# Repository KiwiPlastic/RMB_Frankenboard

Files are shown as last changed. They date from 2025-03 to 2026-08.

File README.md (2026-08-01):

# RMB_Frankenboard

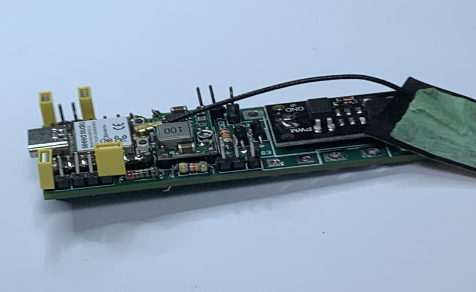
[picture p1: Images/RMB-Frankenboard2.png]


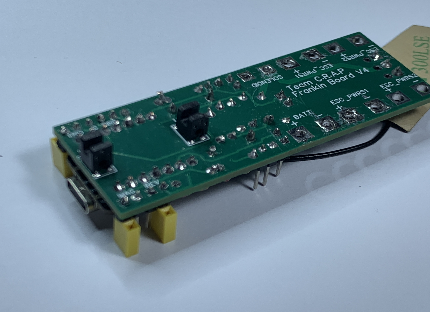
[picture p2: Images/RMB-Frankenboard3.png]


## Introduction
RMB-Frankenboard. A mix of different PCB modules hooked up, flashed and ready to go with a Signal, or Two stage brushless Nerf Blaster type build. Designed to be used with a Neutron solenoid, ramping a 30 dps plus out of the box. Comes with an esp32 MCU and optic gates on the back of PCB for the closed loop feedback.

Controlled and configuration via Blue Tooth app on your phone and a select fire switch on the blaster for fire modes on the go. 
The RMB-Frankenboard can go into any type of Nerf type Blaster with a solenoid, and brushless flywheels. This could be a factory mod, or a 3d printed Blaster.

RMB-Frankenboard is integrated into the newest version of Mjölnir evolved files, which can be found in this repository. 

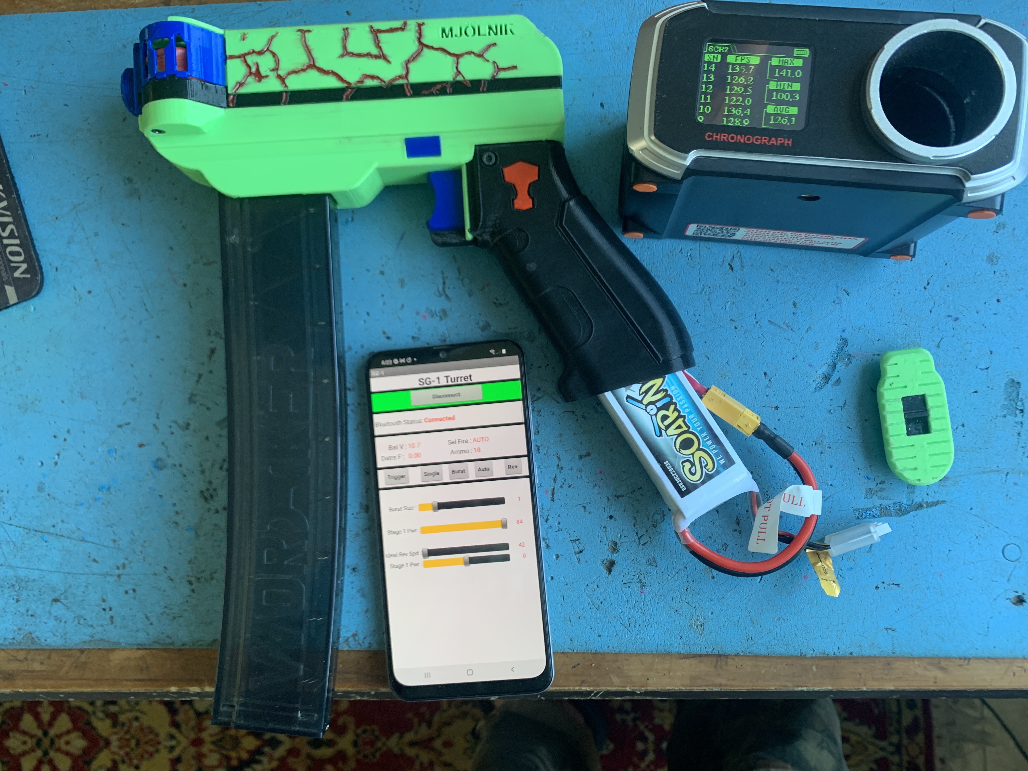
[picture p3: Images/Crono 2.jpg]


RMB-Frankenboard is actively evolving and currently consists of these Features

### Features
- RMB-Frankenboard: Seeed XIAO ESP32C3
- Supports dual Stage Brushless motors wired directly to headers on RMB-Frankenboard
- Will work with Half Darts or Long Darts
- Solenoid Pusher
- Optical Interrupt Gate on PCB for closed loop Pusher feedback. Front and Rear gates
- Single board no wiring loom
- Uses common through Hole parts and modules
- Controlled via Bluetooth App on Android phone for configuring your requirements. Download from google play store
- Battery connects directly to PCB via XT60/30
- Battery Type is auto detected. 4S-2S
- 3 Mode Select fire Switch
- Single Trigger Switch
- Rev Switch
- Magazine Sensor switch (code not completed)

- Via App: Display Battery Voltage
- Via App: Display Select Fire mode
- Via App: Display DPS
- Via App: Display Ammon Counter
- Via App: Trigger Button
- Via App: Game time countdown
- Via App: Burst Size slider
- Via App: Stage 1 Power slider
- Via App: Stage 2 Power slider
- Via App: Rev Ideal Speed slider
- Via App: Game Time slider

### Hardware Required (you supply)
 - 2 x Brushless Motors
 - 2 x ESC or quad
 - Solenoid Pusher (Neutron for Mjolnir evolved) 
 - Trigger switch NO, COM
 - Select fire, 3 position switch, NO, COM, NO
 - Rev Sw NO, COM
 - Mag Sw NO, COM
 - USB type C Data Sync lead

 - Android phone & app for configuration, else is on factory defaults.	
	NOTE: App does not work on iPhone.
	
	NOTE2: Android phone does not need to be connected to a GSM network. Frankenboard uses the phones Blue Tooth for a connection. App can be downloaded to via local Wi-Fi connection.

RMB-Frankenboard Wiring Diagram

## Getting Started - First Power Up
On receiving your RMB-Frankenboard, the first thing to do BEFORE any soldering is started, is to confirm its operation. Do not remove aerial.

First download the repository by clicking the green button over on the right says ‘CODE’ and selecting the zip.
You will also need Arduino IDE and a USB type C data sync cable

Confirm PCB operation in one of two ways: -
- Option 1. Using Phone App. 
Install App on to Android phone from this this link https://play.google.com/apps/internaltest/4701250598279133112
or use APK file in this repository to install App.

	Power up RMB-Franken board, using USB-C lead into a USB power supply or USB on a PC/Laptop
	
	Use App to connect to RMB-Frankenboard and confirm its working by scanning and connecting.

- Option 2. Using Arduino IDE. 
Plug in a USB C data sync lead (Not a charger lead) between RMB-Frankenboard and PC.
Start Arduino IDE and set serial port via tools menu to correct number	
	Open IDE serial monitor window, set board rate to 115200. You should see text output, probably "BAT low.

	If not, close serial window, try reboot by via power cycle (unplug USB lead and plug back in), immediately open serial window open, you should see quite a few lines of text on startup.

Once you have confirmed you have a working board on the bench, you can start your build. 
Install board and solder up.

## Leave one leg of Solenoid disconnected

## Optical Interrupt and Solenoid Duffer
BEFORE powering up...

- Solenoid pusher must have an aligned Duffer attached to it, for the optical interrupts on the solder side of PCB to work correctly.

- NOTE: If this is Duffer is not aligned correctly it will jam and the PCB will smoke and be damaged.

- The Solenoid PCB assembly may need to be pulled apart and put back together a few times to get the operation and tolerances correct.

- On first time assembly the Duffer will be to long.

- Manually move the solenoid in/out, noting where the Duffer touches. 

- Disassemble and file Duffer. 

- Repeat

- Once done correctly you should be able to manually push the pusher out with no resistance along its travel, until it reaches full travel and sits between the front Optic gate.
 
- Let it go slowly, and it should go back to rest between the rear Optic gate. If not dissemble and adjust. If you need to help it, it’s not correct.

- There cannot be the slightest touch between Optic gate and Solenoid Duffer. At high ROF this will course a jam and magic smoke will appear.

- Finaly, hold the pusher in the forward position and let the pusher go, in such a way that it snaps back via the spring. Ensure Duffer goes back through rear Optic gate without collision.

Tech Note: If this is not configured correctly before power up, the RMB-Frankenboard will not function correctly and could burn out.

### BLE Aerial
The BLE Aerial has a very delicate plug, we do not recommend removing it, as it may become damaged and not reconnect to PCB.
Do not power up RMB-Frankenboard without the Aerial connected, this will damage the ESP32 chip, with back RF.

## Power Up and Testing
Once wires are connected, the RMB-Frankenboard needs to be powered from a Li-po battery, to power up correctly. 

The RMB-Frankenboard uses serial output to indicate status.
We can use this to check for correct operation, before using the Trigger.

You will need a Laptop/PC with Arduino IDE running and a USB C type data sync lead, not a charger lead.

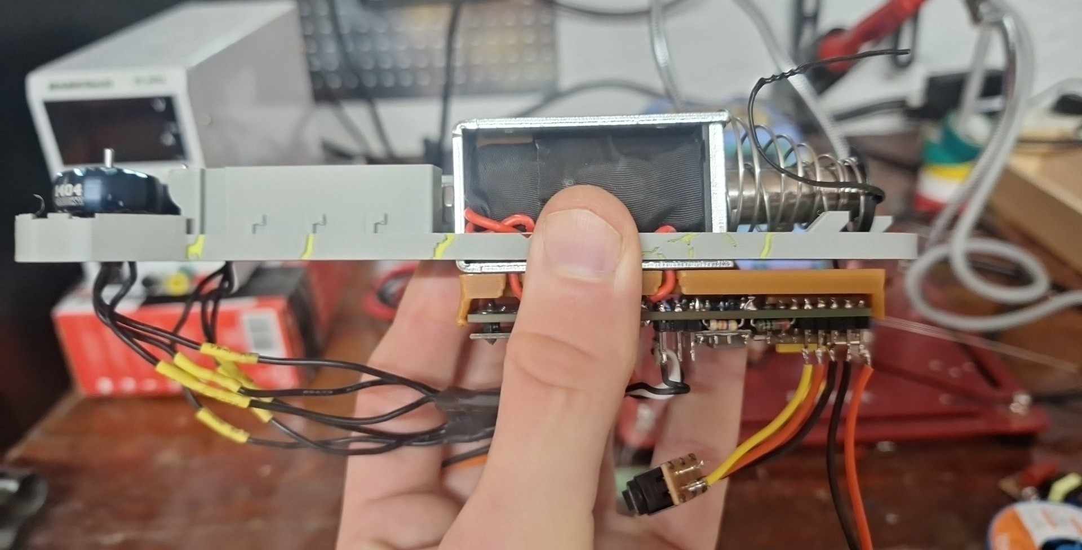
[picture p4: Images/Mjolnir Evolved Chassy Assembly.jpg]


### Plug in Li-Po battery NO USB lead
1. You should here the startup beeps of the ESC's, (Beep, Beep, pause Beep).

2. Plug in USB lead 

3. Start IDE, open serial monitor, and configure com port and baud rate 112500

4. Power cycle RMB-Frankenboard by unplugging USB and plug back in. You should see text data in the IDE serial Window.

5. Change the Select Fire Switch position. Serial Monitor will indicate switch position: - Singal Burst Auto. Leave on Singal.

6. Manually move pusher forward, while watching serial Monitor. 
Rear Optic Gate will indicate 1 and 0, push forward and Front Optic Gate will indicate 1 and 0. If there is resistance, or a tight spot, it needs to be fixed. Disassemble and adjust (file).

7. With Solenoid DISCONNECTED. 
Disconnect USB lead. 
Set Select fire switch to SINGLE shot.
While watching Mosfet pcb, pull trigger once. 
Red LED on Mosfet pcb should light bright and momentary, motors should also spin up.
Try again to be sure.
Do not move the Select Fire Switch
Disconnect battery

8. With battery disconnected, solder other solenoid wire into correct hole on RMB-Frankenboard. NO USB lead.
Reconnect battery
Pull Trigger once
Pusher should snap fast, to do a single shot and flywheels spin.
Try again x 3 or 4 times
Only if that worked, then try Burst, then Full Auto.

Tech Note: 
If something is wrong with the alignment of optic gates and the Dufa, it will do single shot slowly. Burst and full auto will drive Mosfet fully hard on (red led n) making magic smoke if solenoid is connected. 

9. Connect to RMB-Frankenboard via the app, confirm its reading battery voltage eg will be around 12v. 

### RMB-Frankenboard App and Operation
The firmware comes with default configuration setting, and will work fine without the App. 

However, if you want to change the settings or use a remote trigger you will need the app.

The RMB-Frankenboard can be set back to defaults by holding trigger while power up.

If you have purchased an RMB-Frankenboard, you can download the app from this link: -
https://play.google.com/apps/internaltest/4701250598279133112

Alternatively, the apps, apk file is also in the repository and can be installed directly to the phone.

The Android phone does not need to be connected to a GSM network. Frankenboard uses the phones Blue Tooth for a connection, not the GSM network. 
The App can be installed via local Wi-Fi connection.

The App displays status for Battery Volts, Select Fire Mode, Darts Shot,
Trigger and Start (Game Start).

### Slider Settings: -
- Burst Size
- Stage 1 ESC Power
- Stage 2 ESC Power
- Ideal Rev Speed
- Game time

In addition to Trigger and Select Fire switches the RMB-Frankenboard, supports a Rev switch and Mag switch input

### Rev Idel function
Set Ideal Rev Speed > motor stall speed for pre spin. 
First shot will activate ideal, ie its idling after the first shot
Change Select fire Mode Switch to turn ideal off until next shot

If you have a rev button it works like normal, hold it in for on.

## Fault finding
The RMB-Frankenboard has a event based serial output that can be monitored via the serial window in Arduino IDE at 15200 baud.

The serial output can be used to see that buttons, switch's etc are working.

If you cannot see the serial output, there's something not right. Power down. Does it give serial output when powered from USB only? Ie no Li-Po Battery.

## Word of warning
When you have the USB plugged in, DISCONNECT the solenoid or do not operate the trigger. 
The solenoid generates back EMF and can damage the USB port, I speck form experience.

Do not power up RMB-Frankenboard without the Aerial connected, this will damage the ESP32 chip with back RF.

This project is underdevelopment and actively evolving, please report issues so we can make improvements.

## How to Purchase RMB-Frankenboard
RMB-Frankenboard is $35usd plus shipping. 
Most countries, shipping is about $15usd (Ozy is cheaper).

Place order by contacting us via, 
Discord: Kiwi_7862
FB Messenger: Richard Fred

We require these details
- Name:
- Quanty:
- Email Address:
- Delivery address:
- Country:

We will send reply of receipt of your order
Then confirm shipping cost and send you a PayPal invoice via your email
Your email address is also used to register the Android App so u can download it from app store via supplied link. 
On receipt from PayPal that you have paid we ship.
We plan to have an Esty store shortly to make this more simple

## Flash Download Tool
This tool allows flashing of the firmware via *.Bin files.
It is a lot simpler than getting the correct libarys and a working compile from the Arduino IDE.

Firmware upgrades will be done using this tool.

The sub folder \bin in Flash download tool has the *.bin files it it.

Procedure: -
- Disconnect Li-Po Battery
- Close Arduino IDE
- Plug in USB data sync cable (not a charging cable)
- Open Flash Download Tool
- First Window Select: -
-   ESP32 C3
-   Development
-   USB

With reference to screen shoot in folder
Setup the download window. With correct path, and in this order.

 - Bootloader.bin 		0x0
 - Partions.Bin 		0x08000
 - RMB ESP32 V35.Bin 	0x010000

- 40Mhz 
- DIO
- DoNotChgBin = off
- Combine = off
- Select com port at 115200

Put chip in Bootloader mode. 
The chip has two buttons, one each side of the Arieal socket.
One is Reset = R, other is Boot = B
- Unplug USB
- While holding the B boot down plug the USB back in
- It will now power up in Bootloader mode
- Click Start…wait for green bar to move across screen
Flashing Complete

## Links
https://play.google.com/apps/internaltest/4701250598279133112

Note your email needs to be registered with us before this will work

https://github.com/KiwiPlastic/RMB_Frankenboard

https://www.arduino.cc/en/software/

## Attributions
(c) 2019-2021 Michael Ireland / Ireland Software / Airzone for example code used early on in project development work.
BLE Server examples
    Based on Neil Kolban example for IDF: https://github.com/nkolban/esp32-snippets/blob/master/cpp_utils/tests/BLE%20Tests/SampleNotify.cpp
    Ported to Arduino ESP32 by Evandro Copercini
    updated by chegewara and MoThunderz
	
## Licensing
Non-commercial license is in effect. This license flows to derivative works.
You are free to remix / modify the blaster as you see fit. Please share
If you post a remix, please link back to the original.
Commercial use is allowed with the purchase of a RMB-Frankenboard at a ratio of one board = one commercial build.

## 📜 License
RMB-Frankenboard
by Team C.R.A.P is licensed under the Creative Commons Attribution - Non-Commercial Licence. Zero v1.0 Universal License. See `LICENSE` for more information.

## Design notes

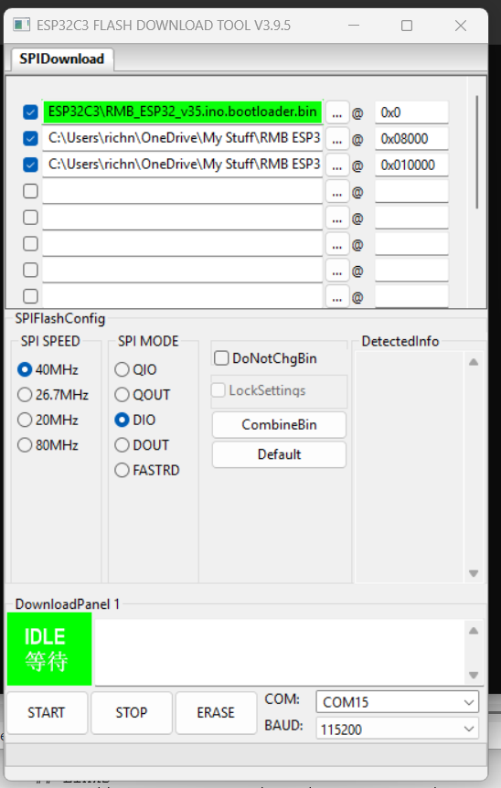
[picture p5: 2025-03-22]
Code/flash_download_tool_3.9.5/Flash downlaod tool.png

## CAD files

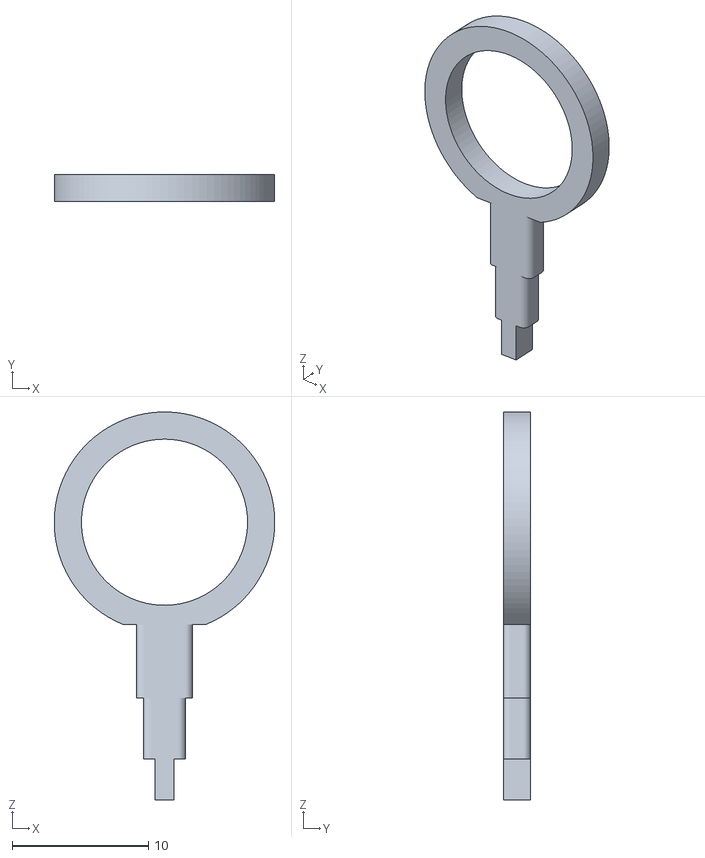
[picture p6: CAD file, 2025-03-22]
3D Prints - Mjolnir Evolved/Solenoid ring By Genexis.stl
16.2 x 2.00 x 28.5

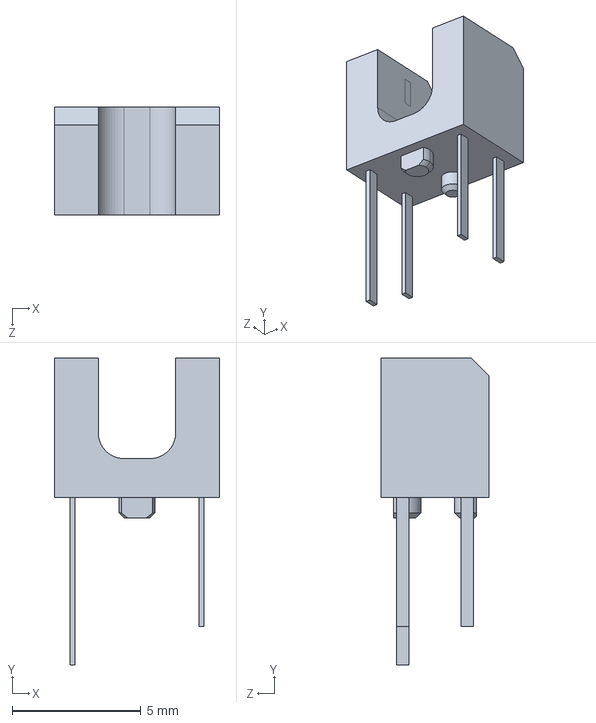
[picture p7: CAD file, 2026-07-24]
PCB/RPI-352.STEP
6.40 x 11.9 x 4.20 mm

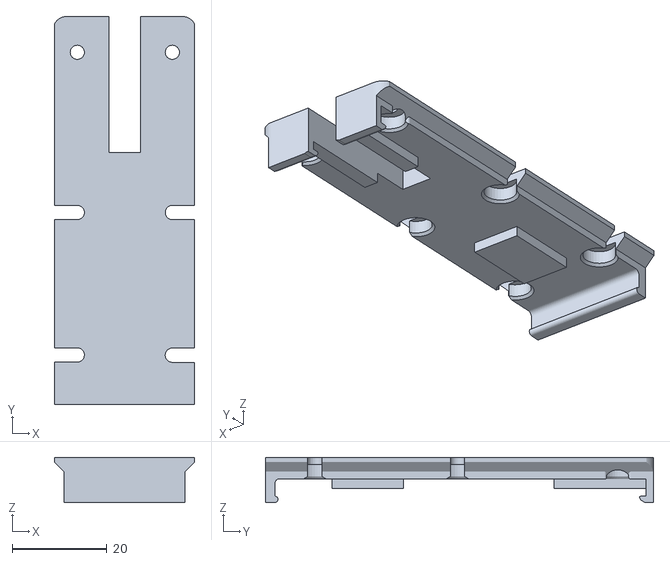
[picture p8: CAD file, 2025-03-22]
3D Prints - Mjolnir Evolved/Solenoid mount by Genexis.stl
29.5 x 81.8 x 9.50

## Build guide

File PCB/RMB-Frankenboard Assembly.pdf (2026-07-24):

## Team C.R.A.P RMB – Frankenboard

What is it
RMB-Frankenboard. A mix of dierent pcb modules hooked up, flashed and ready to go with a brushless build. Ment to be used with a neutron solenoid ramping a 30 dps out of the box. Comes with an esp32 MCU and optic gates on the back for the feedback. Controlled via BT app on your phone and a select fire switch on the blaster for fire modes on the go.
Integrated into the newest version of Mjölnir evolved

Features
- 2 Stage Brushless motors wired directly to RMB-Frankenboard
- Foam Projectiles, Half Darts or Long Darts you could also potentially use rival balls or disks
- Solenoid Pusher
- Optical Interrupt Gate on PCB for closed loop Pusher feed back. Front and Rear gates
- Single board no wiring loom
- Uses common through hole parts and modules
- Controlled via Bluetooth App on Android phone for configuring your requirements. Download from google play store
- Battery connects directly to PCB via XT60/30
- Battery Type is auto detected. 4S-2S
- 3 Mode Select fire Switch
- Single Trigger Switch
- Rev Switch
- Magazine Sensor switch (Future program upgrade)
- Set to defaults by holding trigger while power up
- Via App: Display Battery Voltage
- Via App: Display Select Fire mode
- Via App: Display DPS
- Via App: Display Ammon Counter
- Via App: Trigger Button
- Via App: Game time countdown
- Via App: Burst Size slider
- Via App: Stage 1 Power slider
- Via App: Stage 2 Power slider
- Via App: Rev Ideal Spd slider
- Via App: Game Time slider
- To be added to app: Select fire Switch
- To be added to app: Rev Button
- NOTE: The App, does not work on a iPhone, it’s very expensive to get a dev licence.

Licensing
Non-commercial license is in eect. This license flows to derivative works.
Commercial use is allowed with the purchase of an RMB-Frankenboard from our Store at a ratio of one board = one commercial build.

Attributions
BLE Server examples
Based on Neil Kolban example for IDF: https://github.com/nkolban/esp32-snippets/blob/master/cpp_utils/tests/BLE%20Tests/SampleNotify.cpp Ported to Arduino ESP32 by Evandro Copercini
Updated by chegewara and MoThunderz
(c) 2019-2021 Michael Ireland / Ireland Software / Airzone for example code used early on

License
RMB-Frankenboard
by Team C.R.A.P is licensed under the Creative Commons - Attribution - Non-Commercial Licence
https://creativecommons.org/licenses/by-nc/4.0/

Introduction
This is an advanced project, which requires some experience in electronics to complete. You can purchase the Assembled and tested RMB – Frankenboard from our website site, we recommend this, to minimize frustrations in getting it going.
Please read, all documentation before starting this project.
Documentation:
- Frankenboard assembly, This file.
- RMB_ESP32_vnn.ino Arduino file. Read the header,.
- README.TXT, for helpful information.

FLASHING the ESP32 chip
Before starting this project, you need to flash the ESP32 chip, brand new out of the packet, while it has no wires or soldering done to it. This is very important, as you need to know the chip is working before you solder to it.
If you are not familiar with this procedure for the ESP32, we suggest you purchase the chip only before any other parts. Then flash the chip with the Arduino file.
NOTE you need a Micro USB-C with DATA SYNK cable. Not a phone charger cable.
Basic procedure: -
- Install Arduino IDE
- Load correct Board Library, XIAO ESP32 - S3, or XIAO ESP32 – C3
- Load required library’s, into IDE for the code to compile. It will tell you what libarys it wants
- Get a successful compile
- Upload code (Flash chip)
After flashing, check for serial output in the IDE serial window, 115200 Baud, it will say BAT LOW.
If you get to this point, you have proven you have a ‘working’, RMB ESP32 chip.
Connect Blue Tooth aerial, load app to Android phone, Test app connection and operation.

If your having trouble flashing the ESP32, we recommend buying the assembled RMB-Frankinboard from our webpage.

BOM

### 1 x Micro USB-C Data Sync lead

### 1 x RMB-Frankenboard PCB 77 x 27mm 4 Layer

### 1 x U1 – Seeduino Xiao ESP32-S3. (C3 will work but is significantly slower)

### 1 x U2 - LR7843 Mosfet module

### 1 x U3 - MP2307DN 17x12mm Mini Buck, 5v (adjustable ones can vibrate and might be

unreliable).

### 2 x U4, U5 – RPI-352 Optical Interrupter

### 2 x IN4007 Diodes D1, D2

### 2 x 22K Resistor R5, R8

### 2 x 330R Resistor R3, R6

### 1 x 47K Resistor R1

### 3 x 10K Resistor R2, R4 & R7

### 1 x XT60 Male plug

### 40 x 1 Pin Header Strip

The ESP32, Buck, and Mosfet module, mount via soldered pin headers.
The PCB is laid out to take standard size sockets and plugs.
Plugs and sockets introduce an unreliability in our finished product. I prefer to solder all wiring connections except the ESC signals. I use a 2-pin header for the ESC1 and ESC2 parts, as the ESC normally has a 2 or 3 pin socket on its lead.

Assembly
At this point you should have a Firmware flashed RMB-ESP32
The order of putting parts on this PCB is important, as they go on both sides, and some solder points will not be accessible when other parts are mounted. All leads going through the PCB should be cut as short as possible.
Bottom side
Install the 2 x RPI-352 Optical Interrupter (Note the orientation). The bevelled corner faces the USB-end of the PCB.
The component on the KY-010 interrupter module can be used, if you remove it

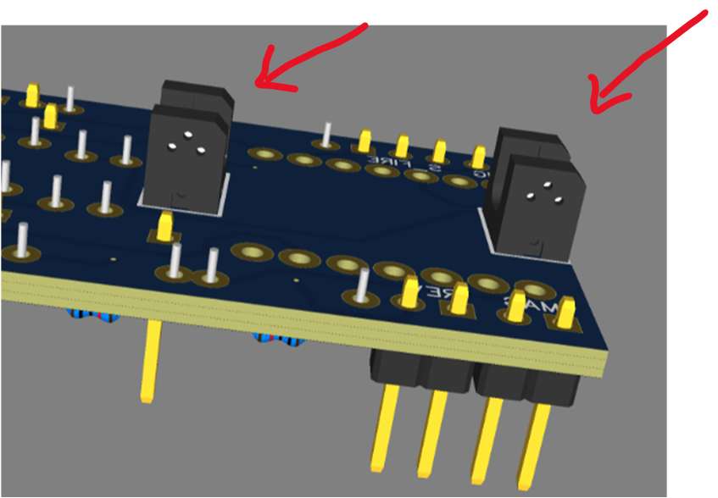
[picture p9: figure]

Top Side

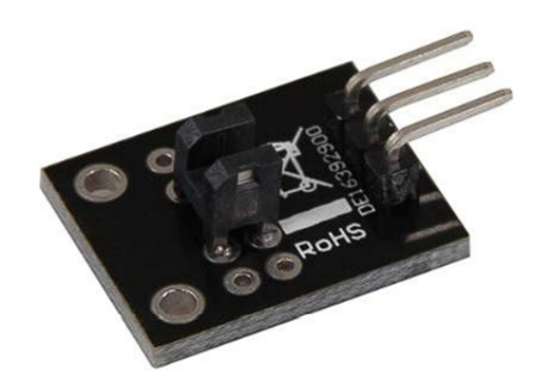
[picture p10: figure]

Next install top side resistors and diodes (Note the direction of the diodes). See diagram
below. | Red lines = Limit input test points

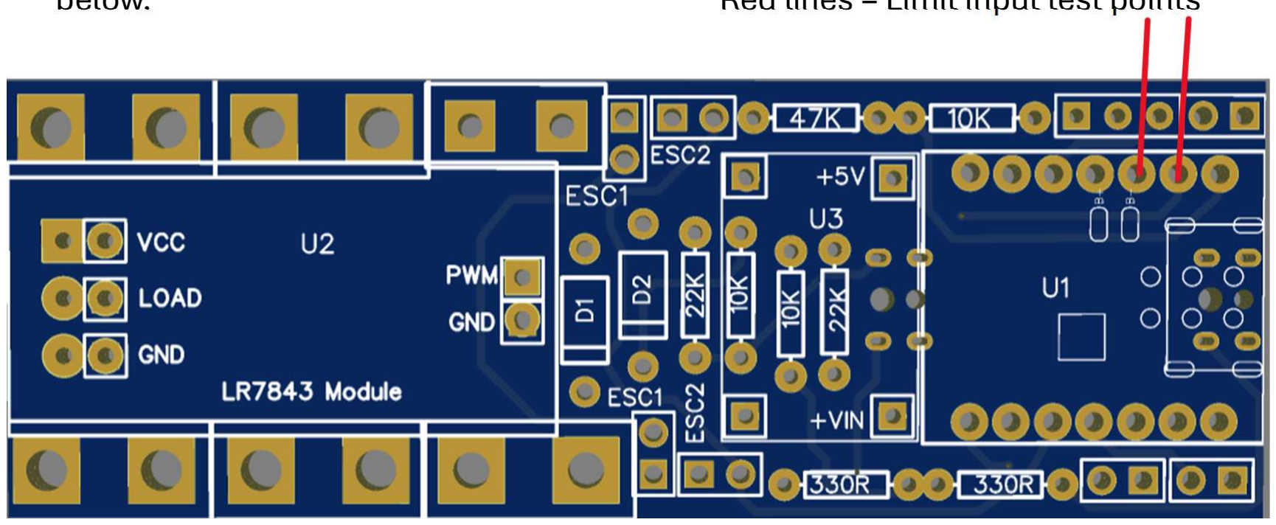
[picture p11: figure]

Mini Buck
This mounts on 4 header pins. Cut 4 single pin headers o pin header strip. Place long end of pin into Frankenboard x 4.
Then place Buck module on top, hold assembly together and solder.
Cut o long legs from underside of Frankenboard.

First Power Up Test 1
Connect a XT60 to the Bat pads (GND on left POS on Right) and plug in Lipo Battery. Using multi meter cheek between GND and 5v pin on ESP32 pad, should be 4-5v.
If Adjustable Buck, set output to ~5.7v as required to get 5.0v at ESP32 5v pin.
Measure between GND and PIN 2 (front limit gate) & PIN 3 (rear limit gate) (see red lines on pic above). Use a bit of tape to slide between interrupters. Voltage will be 0V open and 3V when interrupted
Disconnect battery.
ESP32
This mounts on 2 x 7way pin header strips. Cut 2 strips of 7 pins.
Insert long end of pin header strips into Frankenboard, ESP32 location.
Place ESP32 chip on top. It is keeping the pins in alignment for soldering to the Frankin PCB.
Hold assembly together and solder the pin header to Frankin PCB. Hint solder corner pin first then the rest of the pins. Then solder EPS32 to the pins.
Cut legs o from underside of PCB.
Install Pin Headers: -
Rev/Mag, 4 way
Trigger, 2 way
Select Fire Switch, 3 way
ESC1 and ESC2, 2 x 2 way left hand side, 2 x 2 way right hand side Mosfet Module
This mounts on 5 pins. Cut 1 pair, and 3 single pins
Insert long end of pins into Frankin PCB
Place Mosfet module on top
Do NOT solder Mosfet Module on to any pins, yet.
Hold assembly together and solder pins to bottom side of Frankenboard, only Remove Mosfet Module
Cut legs o from underside of PCB

Power Up Test 2
Do not connect any other wires yet. Do not connect USB to computer yet.
Start Arduino IDE, open serial window at 11520 baud and have USB-C cable ready, DO NOT plug into ESP32 yet.
Connect a Li-Po battery to the XT60 connector, and power up from Li-Po.
Now connect to USB-C and monitor serial window.
Do you have some serial output on screen that is readable.
Using Jumpers, on the pin headers, observe serial output and test:-Trigger Switch
Mag Switch
Rev Switch
Select Fire Mode
Remove USB cable first then lipo Battery. Final wiring
Insert Mosfet Module onto its pins and solder. Connect ESC power cables and Solenoid.
ESC Configuration
The RMB - Frankenboard accommodates Single stage and Dual stage Flywheel/ESC configurations.
Single stage
Simply plug each ESC signal cable into the connections for ESC1 on LHS and ESC1 on RHS. Solder power wires into ESC Pwr connections.
Dual Stage
As above plus, ESC2 on LHS and ESC2 on RHS. Solder power wires into ESC Pwr connections.
The RMB – Frankinboard is tested for up to XX amps, 14 volts 4S lipo battery.
Final Power Up Test 3
Hold trigger down while you connect lipo battery. This clears and defaults the memory settings.
All going well you will hear the startup beeps of your ESC’s.
Using a jumper, on the select fire pins put it into single fire mode (jumper on furthest pins from USB).
Momentarily try a trigger test. Mosfet led should turn on.

Wheels should spin and solenoid will fire.
If this doesn’t happen, it would indicate a fault. Disconnect the battery and start searching for the fault.

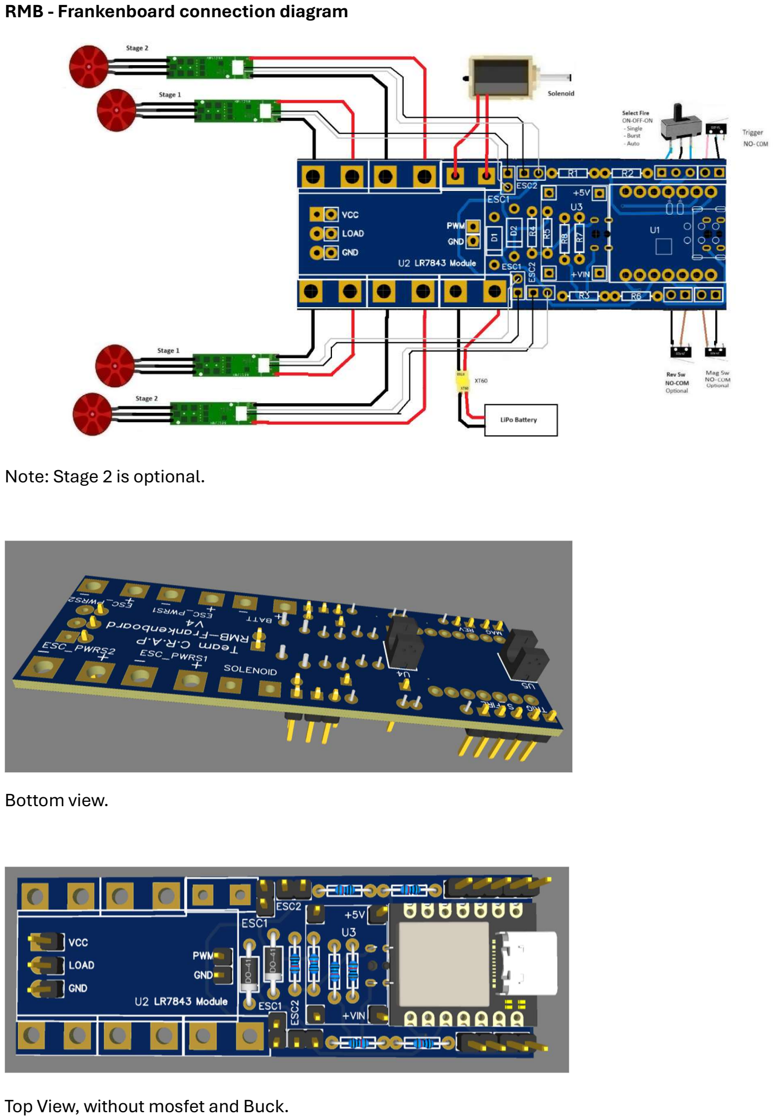
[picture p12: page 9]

RMB - Frankenboard connection diagram

Note: Stage 2 is optional.

Bottom view.

Top View, without mosfet and Buck.

RMB-Frankenboard Schematic:

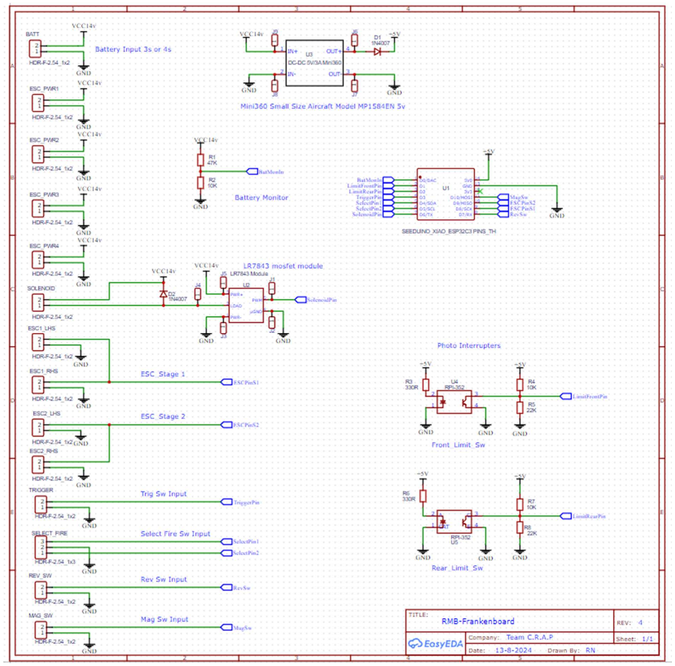
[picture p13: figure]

Flashing the ESP32 when fully wired
To ensure that the chip is in the correct boot mode please use this procedure: The chip can appear to have stopped working if not done correctly.
1. Power up RMB-Frankenboard by Lipo battery.
2. Plug in USB Cable.
3. Start IDE and chk for serial coms is present. Pull the trigger.
4. Unplug the Lipo battery.
5. In IDE select download, program will compile and download.
6. Select serial coms and check output. First line on boot is the version number.
7. Unplug USB.
8. Plug in Lipo and test.

Alternative Limit Switch wiring
If you need to use physical limit switches. This can be accomplished by removing the Photo Interrupter gates, and connecting two wires to the pads indicated, to go to limit switch front and back.

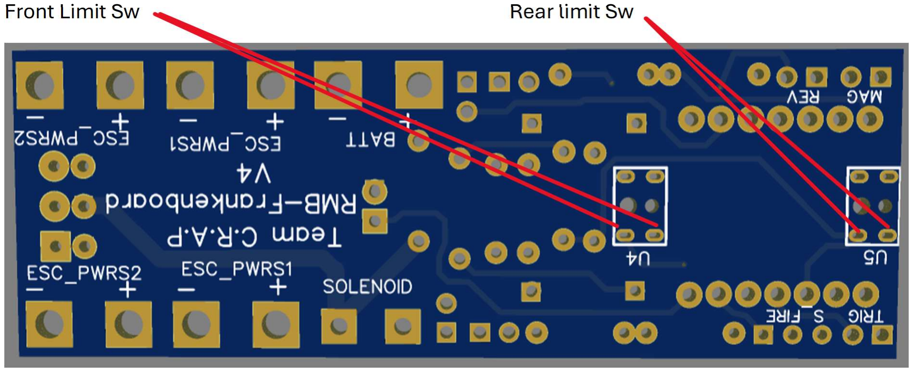
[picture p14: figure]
Front Limit Sw; Rear limit Sw

Useful Links

XIAO ESP32-S3
https://www.seeedstudio.com/XIAO-ESP32S3-p-5627.html

XIAO ESP32 -C3
https://www.seeedstudio.com/Seeed-XIAO-ESP32C3-p-5431.html

Mini Buck, 5v (Do not get adjustable) https://www.aliexpress.com/item/1005006486270630.html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

RPI-352 Optical Interrupter https://www.aliexpress.com/item/1005005805132173.html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 14ad0a98656d2fa166d47-1725070500008-06900-_mqhl1uU&tt=MG&fbclid=IwY2xjawE_W_NleHRuA2FlbQIxMAABHcbLkNNCJgfF3SDu6Kb4BOW r-iAxv--
OOrpo1Etl7_rb7eyO5_8E4jNRHw_aem_Lnkp_anG8G9avq1Bz7w9yQ&a_fsk=_mqhl1uU&a_pl atform=default&sk=_mqhl1uU&a_trace_key=225def8a69d14ad0a98656d2fa166d47-1725070500008-06900-
_mqhl1uU&shareId=21610518952&businessType=ProductDetail&platform=AE&terminal_id=18 184d2796b14b49999ce2660aa4400a&afSmartRedirect=y&gatewayAdapt=4itemAdapt

KY-010 Optical Interrupter can be used by removing part https://www.aliexpress.com/item/1005006290314720.html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 geLogUid=0fXz8dX2Bgrf&utparam-url=scene%3Asearch%7Cquery_from%3A

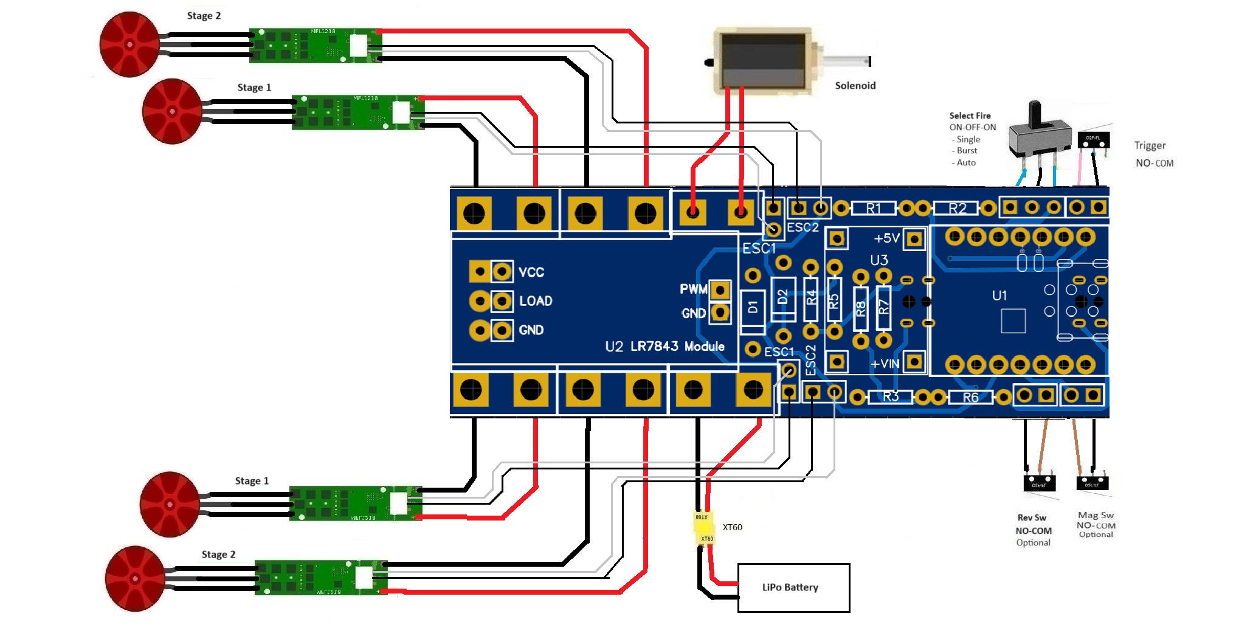
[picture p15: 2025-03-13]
Images/RMB-Frankenboard Wiring Diagram.png

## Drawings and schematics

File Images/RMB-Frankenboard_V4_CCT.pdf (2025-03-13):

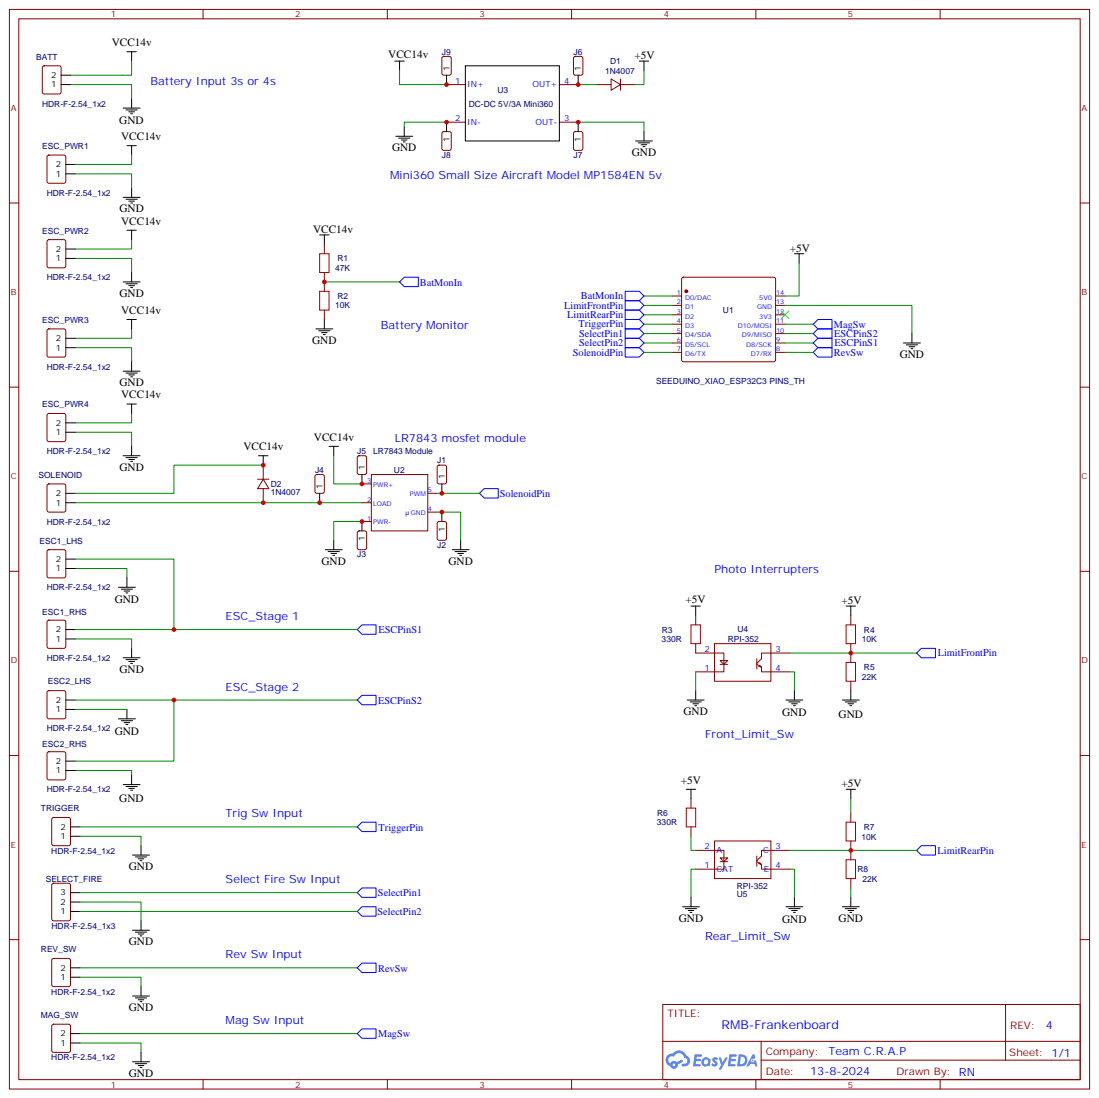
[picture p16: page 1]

GND
Mini360 Small Size Aircraft Model MP1584EN 5v

Select Fire Sw Input

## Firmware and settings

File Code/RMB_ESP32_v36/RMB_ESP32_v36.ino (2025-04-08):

#define VERSION 36
/* 8-4-25

RMB written By RICHRD NICHOLSON from NEW ZEALAND

Licensing

Non-commercial license is in effect. This license flows to derivative works.
You are free to remix / modify the blaster as you see fit. Please share.
If you post a remix, please link back to the original
Commercial use is allowed with the purchase of a RMB-Frankin-board at a ratio of one board = one commercial build

Attributions
(c) 2019-2021 Michael Ireland / Ireland Software / Airzone for example code used early on
For BLE Server examples
    Neil Kolban example for IDF: https://github.com/nkolban/esp32-snippets/blob/master/cpp_utils/tests/BLE%20Tests/SampleNotify.cpp
    Ported to Arduino ESP32 by Evandro Copercini
    updated by chegewara and MoThunderz

License
RMB-Frankin Board
by Team C.R.A.P is licensed under the Creative Commons - Attribution - Non Commercial Licence
https://creativecommons.org/licenses/by-nc/4.0/

Summary
  This code is for a Signal, or Two stage Brushless Nerf type Blaster. Using a solenoid pusher with closed loop feedback sensors
  It uses a three position switch for select fire
  Configuration is via a Android phone app

Hardware
 - Seeed XIAO ESP32C3 or Seeed XIAO ESP32S3
 - Brushless 
 - Solenoid Pusher 
 - Single-Stage Trigger 
 - 2 x limit Switch's,  to make closed loop Solenoid = High ROF
 - Select fire, 3 position switch
 - Mofet PCB, for Solenoid
 - 2 x ESC
 - 1 x Buck voltage regulator

 - Android phone app (BLE Server) does not work on iPhone

Getting Started:
  This is an advanced project. 
  We recommend Flashing the ESP32 before doing anything else. This can save you money
  If you can not get this done you wont move forward.

  NOTE: You need a USB lead that supports data, NOT a phone charger lead which do not transfer data and are common

  https://wiki.seeedstudio.com/XIAO_ESP32C3_Getting_Started/

  Arduino IDE 2.2.1
  Select Board Manger, from menu on left of screen (2nd one down)
  look for esp32 by Espressif Systems, select install, could take a little while 
 
  Libary for ESC's:
  Select Libaray manager, from menu on left of screen (3rd one down)
  Type in ESP32, then scroll down and look for ESP32Servo By Kevin Harrington
  Alternative Method:
  https://github.com/Dlloydev/ESP32-ESP32S2-AnalogWrite
  Download and install via Sketch/Include Libary/Add .Zip Libary

  Libary for PCF8575 Expander:
  Select Libaray manager, from menu on left of screen (3rd one down)
  Typ in Adafruit PCF8574 then select it 
  Alternative Method:
  https://github.com/adafruit/Adafruit_PCF8574
  Download and install via Sketch/Include Libary/Add .Zip Libary
  
*FLASH ESP32 - No WIRES connected
  It is highly recommended that you flash the firmware before you wire anything up to ensure you have a working chip
  This firmware has feature select options, please read past the libary files to see options

  While the chip has no wires on it, it will start and work with the phone app
  Bat Flat on the Serial Monitor (115200 baud) is RMB looking for the 2s/3s/4s battery on D0, Put 47k/10K on and a Bat and it will work
  The code works out what Type your battery is

*FLASH ESP32 WIRES connected
  Once wired with ESC etc... 
  Power from LiPo Bat, FIRST, then plug in USB to laptop
  The ESP32 will not start if the ESC are not powered up first, ie plugging in a USB first is a fail. Its a bootstrapping thing
  Ensure the MOSFET/Solenoid is disconnected. before Flashing firmware, it can activate and possibly make magic smoke

  Other Notes
  The Phone app has a demo mode switch so it can show the connected screen, when its not connected

  Mosfet (pusher output D10)  must be a 2-3v Gate. 5v gate ones will not work

  D8/D9 Bootstap pins must be high at Power Up/Boot
  We are using Boot strapping pins for ESC output,
  ESCs need to be powered up to get a boot if there signal wires are connected to ESP32. Else will look dead.
  Can be powered up with no ESC's if signal wires are not connected

  BLE (Bluetooth Low Energy) this is different to the older Blutooth 2.0 serial and not compatableSupports Rev Ideal mode, set RevIdeal >90 for pre spin. Change Select fire Mode Switch to turn off RevIdeal


 
  //------------------ Dev Notes -----------------------------------------------------
   ESC HW
    ESC frq = 48Khz
    ESC min Trotel = 1040 (1 milisecond)
    ESC Max Trotel = 1960  (2 Millisecond)
    8 bit PWM resolution 0 = 254

   PWM Values for this code
   freq = 1000. 1kHz dont no why, but it works
    42 = off
    45 is lowest ideal speed, lower stalls
    84 is highest speed = ESC Max Trotel, can make number higher but it does  not go any faster

  //------------------------------------------------------------------------------------------------------------------------------------------------
*/
//================================================================================================================================
//Load libraries

#include <ESP32Servo.h>                  // ESC  libary by Kevin Harrington 
ESP32PWM ESC1pwm;                        // 
ESP32PWM ESC2pwm;                        // 

#include <BLEDevice.h>                   // Blue Tooth Libary
#include <BLEUtils.h>
#include <BLEServer.h>
#include <BLE2902.h>

#include <Preferences.h>                 // ESP flash Storage Libary
Preferences preferences;


//==================================================================================================================================================
//               DEFAULT SETTINGS - USER EDITABLE DEFAULT VALUES - Saved to Flash, as default blaster settings. Hold down trig at power up

#define BURST_SIZE 4            // Burst Mode Size #number of darts
#define MOTOR_ESC1_PWR 84       // Stage 1 : ESC1 Defualt Setting Range: 45-84 max
#define MOTOR_ESC2_PWR 84       // 42 = Stop, 45 = Slow idel Rev, 84 = Full Speed
#define MOTOR_REV_IDEAL 42      // 42 = Stop, 45 = Slow idel Rev, 84 = Full Speed
#define MOTOR_MIN_SPEED 45      // 42 = Stop, 45 = Slow idel Rev, 84 = Full Speed

#define BATTERY_CALFACTOR 1.0   // Adjustment for battery calibration calibration

#define PUSHER_MAX_T 80         // ms for pusher error detect

#define MIN_DWELL_TIME 1        // NOT USED YET WIP
#define AMMO_COUNTER 18         // Mag Size, NOT USED YET WIP

//====================================================================================================================================================

//--------------------------------------------------------------------------------------------------------------------------------------
// Seeed ESP32 C3 or ESP32 S3 -  Pin Definitions (BIOS)
//--------------------------------------------------------------------------------------------------------------------------------------

#define PIN_BATT_MON A0     // Bat Volts  A0/D0       IP           Analog LiPo battery reading, Resistor devideder 47K/10K
#define PIN_PUSHER_F D1     // Pusher Limit Sw Front  IP
#define PIN_PUSHER_R D2     // Pusher Limit Sw Rear   IP
#define PIN_TRIGGER D3      // Trigger                IP
#define PIN_SELF_A D4       // Select Fire A Sw       IP
#define PIN_SELF_B D5       // Select Fire B Sw       IP
#define PIN_MAG_SW D6       // Mag switch             IP           D6 should be used as O/P only, to do with boot straping - testing mag sw option
#define PIN_REV_SW D7       // RevSw   PB             IP
#define PIN_ESC_1 D8        // Stage 1 ESC output     OP           ESC Stage 1  D8 is a boot strap pin. must be high at startup
#define PIN_ESC_2 D9        // Stage 2 ESC output     OP           ESC Stage 2  D9 is a boot strap pin. must be high at startup
#define PIN_RUN D10         // Pusher                 OP           moved from D6 due to pin current failures

//----------------------------------------------------------------------------------------
//Motors 
int MinMotorSpeed = MOTOR_MIN_SPEED;       //
int MaxMotorSpeed1 = MOTOR_ESC1_PWR ;      //
int MaxMotorSpeed2 = MOTOR_ESC2_PWR ;      //

// Battery Controls
#define BATTERY_2S_MIN 6.4                 //
#define BATTERY_3S_MIN 9.6                 //
#define BATTERY_4S_MIN 13.2                //
float BatteryCurrentVoltage = 99.0;        //
float BatteryOffset = BATTERY_CALFACTOR;   // asign to a floating point veriable so can be adjusted in config menu (work in progress)
float BatteryMinVoltage = BATTERY_2S_MIN;  // this is just to load the float with a value
bool BatteryFlat = false;

// ISR Flags
bool ISR_PUSHER_F_Flag = false;            // Interrupt triggered flag
bool ISR_PUSHER_R_Flag = false;            // Interrupt triggered flag
bool ISR_TRIGGER_Flag = false;             // Interrupt triggered flag
bool ISR_SELF_A_Flag = true;               // Interrupt triggered flag
bool ISR_SELF_B_Flag = true;               // Interrupt triggered flag
bool ISR_REV_SW_Flag = false;              // Interrupt triggered flag
bool ISR_MAG_SW_Flag = false;              // Interrupt triggered flag

// System Modes
#define SYSTEM_MODE_NORMAL 0               // Ideal/ok to Fire
#define SYSTEM_MODE_LOWBATT 1              // All stop
#define SYSTEM_MODE_FLYWHEELFAIL 2         // not used wip
byte SystemMode = SYSTEM_MODE_NORMAL;      //

// Firing Controls
#define ONESEC 1000                        // One second

//Selectfire 
#define AUTO 0
#define BURST 1
#define SINGLE 2
byte CurrentFireMode = SINGLE;
volatile bool SF_Changed_Flag = false;    // Select Fire Changed
volatile bool MotorRunningFlag = false;   // 

// Inputs
#define DebounceWindow 5                  // Debounce Window = 5ms   **** CHK
#define RepollInterval 250                // Just check the buttons ever xxx just in case we missed an interrupt. 

// Input Button Status, For ISR output
#define BTN_LOW 0
#define BTN_HIGH 1
#define BTN_ROSE 2
#define BTN_FELL 3

// main internal registers/veriables
byte TriggerButtonState = BTN_HIGH;
byte BLETriggerButtonState = false;
byte BLE_SF_PB_State = false;
byte BLERev_PB_State = false;
byte BurstSize = BURST_SIZE;
byte ESC1_Pwr = MOTOR_ESC1_PWR;
byte ESC2_Pwr = MOTOR_ESC2_PWR;
byte RevIdeal = MOTOR_REV_IDEAL;
//float DPS_Value = 0;                        // calculated value by firing ctrl repported by nofify

// Map Flash Memory loads defaults on start up, if not exist
unsigned int burstsize = BURST_SIZE;        //
unsigned int esc1 = MOTOR_ESC1_PWR;
unsigned int esc2 = MOTOR_ESC2_PWR;
unsigned int revideal = MOTOR_REV_IDEAL;

volatile bool DefaultFlag = false;          // Default flash stroage values
volatile bool PusherTickTock = false;       // To capture the first edge of each pusher in / out cycle

volatile bool PusherFront = false;          // Status flags for manual testing
volatile bool PusherRear = false;

int stat_LED = 0;                           // status of LED: 1 = ON, 0 = OFF
unsigned long LastBlinkLED;                 // start time in milliseconds


//================================== BLE Server Config ==================================
// Some General Veriables

bool deviceConnected = false;              //
bool oldDeviceConnected = false;           //
unsigned long BLE_TimeConnected = 0;       //
bool NotifyFlag = false;                   // Used by RMB to send Notify to App
char BLEValue[2];                          // used by Callbacks to read characteristics values

uint32_t BatVoltsValue = 0;                //
uint32_t BLE_SF_ModeValue = 0;             //
uint32_t AmmoCounterValue = AMMO_COUNTER;  // <<<< chnage this to get working
uint32_t BurstSizeValue = BurstSize;       //
uint32_t ESC1Value = ESC1_Pwr;             //
uint32_t ESC2Value = ESC2_Pwr;             //
uint32_t RevIdealValue = RevIdeal;         //
uint32_t TriggerValue = 0;                 //
byte CurrentShotValue = 0;                 //


volatile byte LastBatVolts = 99;           //
volatile byte LastSF_Mode = 99;            //
volatile byte LastAmmoCounter = 99;        //
volatile byte LastBurstSize = 99;          //
volatile byte LastESC1 = 99;               //
volatile byte LastESC2 = 99;               //
volatile byte LastRevIdeal = 99;           //
volatile byte LastCurrentShot = 99;        //
//volatile byte LastDPS = 99;                //       possible delete???
volatile byte LastBatteryFlat = 99;        //
volatile byte BLE_LastRev_PB = 99;         //
volatile byte BLE_Last_SF_PB = 99;         //

//------------------------------- BLE Characteristic Labels ------------------------------

BLEServer* pServer = 0;                 // Server Advertising
BLECharacteristic* pStatus_Update = 0;  // Notify Status Update
BLECharacteristic* pTrigger = 0;        // R/W Trigger PB
BLECharacteristic* pSF_PB = 0;          // R/W SF PB value
BLECharacteristic* pRev = 0;            // R/W Rev PB
BLECharacteristic* pBurst_Size = 0;     // R/W Burst Size via slider
BLECharacteristic* pESC1 = 0;           // R/W ESC1 Pwr via slider
BLECharacteristic* pESC2 = 0;           // R/W ESC2 pwr via slider
BLECharacteristic* pRevIdeal = 0;       // R/W Rev Ideal Spd via slider

BLEDescriptor* pDescr;
BLE2902* pBLE2902;

//------------------------ BLE Characteristics UUID --------------------------------------
// See the following for generating UUIDs:
// https://www.uuidgenerator.net/
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
void loop() {
  ProcessDebouncing();                     // Process the Trigger input, and handle any debouncing
  ProcessBatteryMonitor();                 // Check battery voltage occasionally
  ProcessSystemMode();                     // Handle the system mode (Low battery chk)
  ProcessBLESelectFire();                  // Chk Selectfire
  ProcessSelectFire();                     // Chk Selectfire
  ProcessMagSwitch();                      // process Mag switch
  ProcessBLERevSwitch();                   // process Rev switch from BLE
  ProcessRevSwitch();                      // Chk Rev and Mag switch inputs 
  ProcessFiring();                         // Handle any firing here
  ProcessBLE();                            // BLE Server
  ProcessBlinkLED();                       // one sec hart beat ESP32-C3 does not have one
}

//===========================================================================================================
//------------------------------------ Process Debounce - Trigger  -------------------
void ProcessDebouncing() {
  unsigned long CurrentMillis2 = millis();           // Single call to millis() for better performance
  static bool RunTriggerTimer = false;
  static unsigned long LastTriggerPress = 0;
  static byte TriggerDebounceState = 0;
  byte ButtonState = 0;

  // Set up a repoll interval, just in case the interrupt is missed.
  if (CurrentMillis2 - LastTriggerPress > RepollInterval) ISR_TRIGGER_Flag = true;
  // Move from edge to steady state
  if (TriggerButtonState == BTN_ROSE) TriggerButtonState = BTN_HIGH;
  if (TriggerButtonState == BTN_FELL) TriggerButtonState = BTN_LOW;

  if (ISR_TRIGGER_Flag) {
    ISR_TRIGGER_Flag = false;
    if (!RunTriggerTimer) {
      LastTriggerPress = CurrentMillis2;

      TriggerDebounceState = 0b01010101;  // We need to give the button time to settle. This will track.
      RunTriggerTimer = true;
    }
  }
  if (RunTriggerTimer && (CurrentMillis2 - LastTriggerPress > DebounceWindow)) {
    //TriggerDebounceState = (TriggerDebounceState << 1) | ((PIND >> 6) & 0b00000001); // Shift the register pin to the left, Shift the pin result to the right most position, and tack it onto the debounce state. Ensure that only the last position can be a 1.
    TriggerDebounceState = 255;
    if ((TriggerDebounceState == 0) || (TriggerDebounceState == 255))  // All 0's or all 1's. This means we have settled.
    {
      RunTriggerTimer = false;
      ButtonState = digitalRead(PIN_TRIGGER);
      if (ButtonState) {
        if (TriggerButtonState != BTN_HIGH) TriggerButtonState = BTN_ROSE;
      } else {
        if (TriggerButtonState != BTN_LOW) TriggerButtonState = BTN_FELL;
      }
    }
  }
}

//------------------------------------ Process Battery Monitor -------------------------------------------------
void ProcessBatteryMonitor() {
#define NUM_SAMPLES 8
  static byte CollectedSamples = 0;
  static float SampleAverage = 0;
  uint32_t Vbatt = 0;

  if ((SystemMode == SYSTEM_MODE_NORMAL) || (SystemMode == SYSTEM_MODE_LOWBATT))         // Only read if system mode is normal or low batery
  {
    if (CollectedSamples < NUM_SAMPLES) {
      CollectedSamples++;
      SampleAverage += analogReadMilliVolts(PIN_BATT_MON);                               // Read ADC with correction
    } else {
      BatteryCurrentVoltage = ((6 * SampleAverage / 8 / 1000.0) - BatteryOffset);        // attenuation ratio 1/6, mV --> v
      BatVoltsValue = int(BatteryCurrentVoltage * 10);                                   // convert to int for BLE value

      if ((BatVoltsValue > (LastBatVolts + 3)) || (BatVoltsValue < (LastBatVolts - 3)))  // Provide hysteresis
      {
        //BatVoltsValue = BatVoltsValue;                                                 // update, dumy as already loaded above
      } else {
        BatVoltsValue = LastBatVolts;                                                    // dont update
      }

      if (BatteryCurrentVoltage < BatteryMinVoltage) {
        if (BatteryCurrentVoltage > 1.6)                                                 // If the current voltage is 0, we are probably debugging
        {
          BatteryFlat = true;
          Serial.println("BAT FLAT V = " + String(BatteryCurrentVoltage));
          Serial.println("Bat Min = " + String(BatteryMinVoltage));                       //Debug
        } else {
          BatteryFlat = false;
        }
      } else {
        BatteryFlat = false;
      }
      CollectedSamples = 0;
      SampleAverage = 0;
    }
  }
}

//-------------------------------- Process System Mode ---------------------------------------------------------
void ProcessSystemMode() {

  static byte LastSystemMode = 99;
  //static unsigned long LastFlywheelJam = 0;

  if (BatteryFlat) {
    SystemMode = SYSTEM_MODE_LOWBATT;
  } else {
    SystemMode = SYSTEM_MODE_NORMAL;
  }
  LastSystemMode = SystemMode;

  if (SystemMode == SYSTEM_MODE_NORMAL) {              // Optic Gate Readout for testing PCB 
    if (PusherRear == true){
      byte pr= digitalRead(PIN_PUSHER_R);
      Serial.println ("Pusher Rear = " + String (pr));
      PusherRear = false;
    }
    if (PusherFront == true){
      byte pf = digitalRead(PIN_PUSHER_F);
      Serial.println ("Pusher Front = " + String (pf));
      PusherFront = false;
    }
  }
}

//----------------------------------------- Process SelectFire ---------------------------------------------------
void ProcessBLESelectFire() {
  if (BLE_Last_SF_PB != BLE_SF_PB_State) {
    if (BLE_SF_PB_State == BURST) {
      CurrentFireMode = BURST;
      BLE_SF_ModeValue = BURST;             // BLE notify BURST
      Serial.println("Burst Mode");
    } else if (BLE_SF_PB_State == SINGLE) {
      CurrentFireMode = SINGLE;
      BLE_SF_ModeValue = SINGLE;            // BLE notify SINGLE shot
      Serial.println("Single Shot");
    } else {
      CurrentFireMode = AUTO;
      BLE_SF_ModeValue = AUTO;              // BLE notify AUTO
      Serial.println("Full Auto");
    }
    SF_Changed_Flag = true;                 //indicate SF has changed to stop RevIdeal
    BLE_Last_SF_PB = BLE_SF_PB_State;
    //Serial.println("SF PB = " + String(BLE_SF_PB_State)); // Debug
  }
  if ((SF_Changed_Flag == true) && (RevIdeal >= MOTOR_MIN_SPEED) && (MotorRunningFlag == true)) {  // turn off motors if RevIdeal > 42
    MinMotorSpeed = MOTOR_REV_IDEAL;
    SF_Changed_Flag = false;
    MotorRunningFlag = false;
    StopMotors();
  }
  SF_Changed_Flag = false;
}

//----------------------------------------- Process SelectFire ---------------------------------------------------
void ProcessSelectFire(){
  if (ISR_SELF_A_Flag || ISR_SELF_B_Flag)       // if ISR flag set read pins
  {
    byte SFA = digitalRead(PIN_SELF_A);
    byte SFB = digitalRead(PIN_SELF_B);

    ISR_SELF_A_Flag = false;
    ISR_SELF_B_Flag = false;

    if (SFA == HIGH && SFB == HIGH) {
      CurrentFireMode = BURST;
      BLE_SF_ModeValue = BURST;                     // BLE notify BURST
      Serial.println("Burst Mode");
    } else if (SFA == HIGH && SFB == LOW) {
      CurrentFireMode = SINGLE;
      BLE_SF_ModeValue = SINGLE;                    // BLE notify SINGLE shot
      Serial.println("Single Shot");
    } else {
      CurrentFireMode = AUTO;
      BLE_SF_ModeValue = AUTO;                      // BLE notify AUTO
      Serial.println("Full Auto");
    }
    SF_Changed_Flag = true;                         //indicate SF has changed to stop RevIdeal
  }
  if ((SF_Changed_Flag == true) && (RevIdeal >= MOTOR_MIN_SPEED) && (MotorRunningFlag == true)){     // turn off motors if RevIdeal > 42
    MinMotorSpeed = MOTOR_REV_IDEAL;
    SF_Changed_Flag = false;
    MotorRunningFlag = false;
    StopMotors();
  }
  SF_Changed_Flag = false;
}

//------------------------- Process Mag Switch Input ------------------------------------------------------
void ProcessMagSwitch() {
  static byte LastMagSwButtonState = 99;

  if (ISR_MAG_SW_Flag) {
    byte MagSwButtonState = digitalRead(PIN_MAG_SW);            // Read Mag Switch
    if (MagSwButtonState != LastMagSwButtonState) {
      Serial.println("MagSw = " + String(MagSwButtonState));    // debug
      
      //Put handeler code here
      
      LastMagSwButtonState = MagSwButtonState;
    }
    ISR_MAG_SW_Flag = false;
  }
}
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
